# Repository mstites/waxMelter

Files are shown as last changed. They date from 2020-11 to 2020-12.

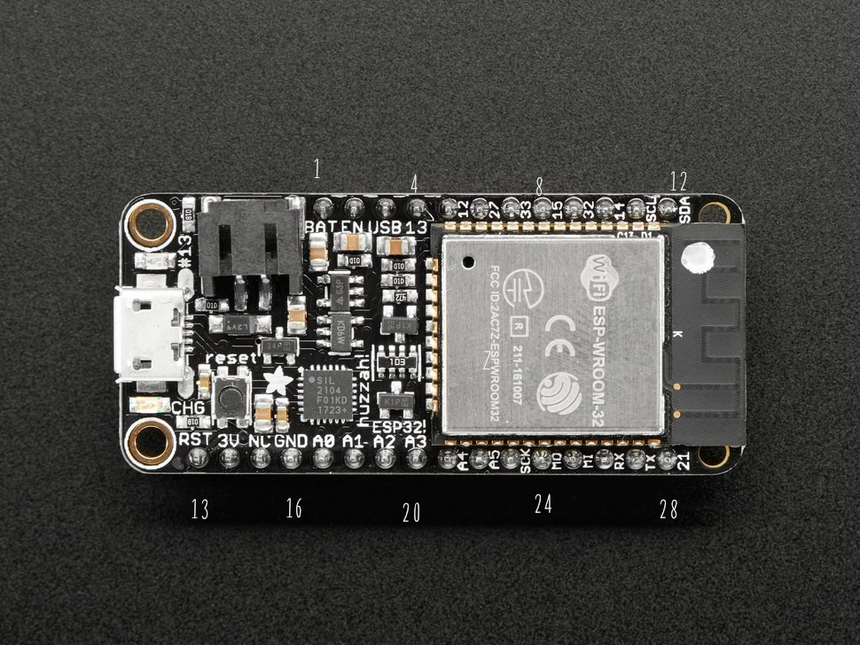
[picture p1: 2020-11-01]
schematic/microNumbering.png

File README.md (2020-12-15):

# waxMelter
Custom designed board and software for a bangbang controlled thermocouple feedback wax melter. Please see [project page](https://www.mstites.com/items/wax_melter.html) for more information.

## Overview
The board heats and maintains the temperature of a container of candle wax via controlling a hot plate with a relay power control. All code was written in C in an Arduino based environment for an Adafruit ESP32 Huzzah. There is a fully functional OLED and button UI and web based UI.

## Files and Notes
* For final software iteration please see [software/dualUi](software/dualUi). Software depends on the [espressif-esp32](https://github.com/espressif/arduino-esp32#using-through-arduino-ide) and [ESPAsyncWebServer](https://github.com/me-no-dev/ESPAsyncWebServer) libraries. Any other missing dependencies should be able to be installed through the Arduino IDE (eg [Button2](https://github.com/LennartHennigs/Button2), [RunningMedian](https://github.com/RobTillaart/RunningMedian)).
* Project proposal is located in [proposal](proposal). This was a project for [ENGR3499-02: Microcontrollers for the Real World](http://reifel.org/realworld/) taught by Stan Reifel at Olin College of engineering. Though this project was also a passion work as I [make many candles](http://trandleboutique.com).
* Final schematic, kicad files, and PCB files are located in [schematic](schematic). It should be noted that the final PCB I ended up with I had to make adjustments to. I had to disconnect the A1 to SENSOR_0 connection and reconnect SENSOR_0 to A2. The same would also have to be done with respect to A5 and SENSOR_1 (to some ADC1 pin). This is because the original pins, A1 and A5, I picked are connected to ADC2 on the ESP. Only ADC1 can be used while wifi is enabled ([see here for pin numbering](https://learn.adafruit.com/adafruit-huzzah32-esp32-feather/pinouts)).

## Parts List
* [Adafruit HUZZAH32](https://www.adafruit.com/product/3591)
* [Thermocouple Amplifier AD8495](https://www.adafruit.com/product/1778)
* [K Type Thermocouple](https://www.ebay.com/itm/1M-K-Type-Thermocouple-Sensor-Digital-Thermometer-Temperature-Meter-TK80-4JPL8/282896189061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)
* [Hot Plate](https://www.amazon.com/gp/product/B07MMT2SC5/ref=ask_ql_qh_dp_hza)
* [Outlet Power Relay](https://www.amazon.com/Iot-Relay-Enclosed-High-Power-Raspberry/dp/B00WV7GMA2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)
* [SPI OLED 128x64](https://www.amazon.com/UCTRONICS-SSD1306-Self-Luminous-Display-Raspberry/dp/B072Q2X2LL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)
* SPST Switch x6
* USB Power Supply
* Micro USB Cable
* LD1117V33 x2	
* 0.1uF Cermic Capacitor x6
* 10uF Electrolytic Capacitor x4
* 4.7K Resistor 1/8W x6
* 2 Pin Screw Terminal x2
Sockets:
* 16 pin x2
* 12 pin x2
* 4 pin x2

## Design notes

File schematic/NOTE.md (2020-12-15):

In my initial design, I did not realize that ADC #2 cannot be used while wifi is on with the ESP32. Both of my analog reads for the thermocouples in my design were on ADC #2. To remedy this in my design, I ran a jumper from SENSOR_0 to A2 and used a knife to take out the A1 path. I did not use the other channel, though a similar remedy could have been implemented.

I recommend in future iterations moving to A2 and A4 instead of A1 and A5 to avoid this issue.

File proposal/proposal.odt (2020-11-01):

Wax Melter Proposal

Maeve Stites

# Overview and Background

I am going to make a board to control a system to heat wax (used in candle making) to a specified temperature. I run a queer and trans candle shop (http://www.trandleboutique.com/) where I make and sell hand poured candles. One of the most variable and frustrating parts of the process is melting the wax. The wax has to be heated to a specific temperature to mix in dyes and scents. The wax is heated to a different temperature to pour into the candle containers. I currently do this over the stove in a double broiler system, where it is hard to regulate temperature. Differences as small as 5 degrees (F) can make a big difference in the performance of the wax.

The board will regulate the container temperature and monitor the temperature of the wax to help it reach the right temperature and stay there. It will control a hot plate, which will heat a container containing the wax. The board will use temperature monitoring, temperature control via a hot plate, and remote control through a web platform.

# Parts List

- Adafruit HUZZAH32 (https://www.adafruit.com/product/3591) - $20.95
- Thermocouple Amplifier AD8495 (https://www.adafruit.com/product/1778) - $11.95
- K Type Thermocouple (https://www.ebay.com/itm/1M-K-Type-Thermocouple-Sensor-Digital-Thermometer-Temperature-Meter-TK80-4JPL8/282896189061) - $5.75
- Hot plate (https://www.amazon.com/gp/product/B07MMT2SC5/ref=ask_ql_qh_dp_hza) - $22
- Outlet Power Relay (https://www.amazon.com/Iot-Relay-Enclosed-High-Power-Raspberry/dp/B00WV7GMA2) - $27
- OLED 128x64 Yellow Blue (https://www.amazon.com/UCTRONICS-SSD1306-Self-Luminous-Display-Raspberry/dp/B072Q2X2LL) - $7
- SPST Switch (https://www.digikey.com/en/products/detail/apem-inc/MJTP1230/1798037) - $0.10 X6
- USB Power Supply (https://www.adafruit.com/product/501) - $5.95
- Micro usb cable – Have
- LD1117V33 (https://www.digikey.com/en/products/detail/stmicroelectronics/LD1117V33/586012) - $0.55 X2
- 0.1uF Ceramic Capacitor (https://www.digikey.com/en/products/detail/vishay-beyschlag-draloric-bc-components/K104K15X7RF5TL2/286538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) - $0.23 X6
- 10uF Electrolytic Capacitor (https://www.digikey.com/en/products/detail/nichicon/UKL1C100KDD1TD/5699141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)- $0.27 X4
- 4.7K Resistor 1/8W (https://www.digikey.com/en/products/detail/stackpole-electronics-inc/CF18JT4K70/1741708) - $0.10 X6
- 2 Pin Screw Terminal (https://www.digikey.com/en/products/detail/phoenix-contact/1751248/2511016) - $1.26 X2
- Sockets - $3.5 total
  - 16 pin (https://www.digikey.com/en/products/detail/sullins-connector-solutions/PPPC161LFBN-RC/810188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) (micro) - $1.02 X2
  - 12 pin (https://www.digikey.com/en/products/detail/sullins-connector-solutions/PPPC121LFBN-RC/810184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) (micro) - $0.81 X2
  - 4 pin (https://www.digikey.com/en/products/detail/sullins-connector-solutions/PPPC041LFBN-RC/810176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) (amplifier and OLED) - $0.47 X2

Total = $111.38

# Implementation Plan

The core of the system is the Adafruit HUZZAH32. I chose this particular micro controller because of its integrated wifi module and common use in IoT device spaces. The ESP32 is an updated version of the popular ESP8266. And has more GPIOs and is faster, and the boards come in around the same price. This last part means there is lots of documentation and support online for communicating with the device over wifi and hosting a web page on the device.

The whole system will be controlled via a locally accessible web page broad-casted by the micro controller (my additional area of study). The website will contain the current temperature reading of the wax/container, the target temperature, and have a buttons for controlling the target temperature for the wax, as well as the power of the device. I am not currently planning on implementing a way to communicate with the micro controller remotely, as the use case of my board – making candles – means the user should be on the same local network.

A secondary user interface will be visible via an OLED panel. This will have temperature readings and target temperature information. The OLED will be connected over I2C. Buttons will be placed below the panel to interact via this secondary user interface.

The system will get temperature readings via the thermocouple connected via the thermocouple amplifier (AD8495). I am planning on building in two thermocouple channels, but only putting in components for one due to cost restrictions. With the one thermocouple, I can regulate the outside temperature of the container or the temperature of the wax. With a second thermocouple, I could also track the internal temperature of the wax in real time while tracking the temperature of the container.

The thermocouple will be connected via a 2 position screw terminal. The thermocouple amplifier will be connected to one ADC input channel.

To control the temperature of the wax, the board will control a hot plate. This will be done by flipping the outlet on and off via the Outlet Power Relay, connected via a digital i/o pin. The specific software implementation will come with time, but a basic bang/bang controller could work with the limits for when to flip the switch determined in testing. Some sort of PID loop could be implemented if this did not work well enough.

All of the modules support 3.3V logic. All power will be supplied by the usb adapter. Power will be stepped down for the micro by the onboard voltage regulator. The LD1117V33 will be used to power the OLED and the thermocouple modules.

### Resources

#### Wireless

Connecting ESP32 to Wifi Networking (https://circuits4you.com/2019/01/05/connecting-esp32-to-wifi-network/)

ESP32: Getting Started with Wifi (https://www.dfrobot.com/blog-948.html)

ESP32: Set Static IP (https://techtutorialsx.com/2020/04/21/esp32-arduino-set-static-ip-address/) (shouldn’t be necessary, but this resource has more wireless info)

#### Web

Controlling RGB Lights from ESP32 (https://diyusthad.com/2019/10/controlling-rgb-lights-from-esp32-web-server.html)

ESP32-CAM Take Photo and Display in Web Server (https://randomnerdtutorials.com/esp32-cam-take-photo-display-web-server/)

#### Thermocouple

Wiring a Thermocouple (https://learn.adafruit.com/thermocouple/wiring-a-thermocouple)

Power and Temperature Data Logger with ESP32 and AWS IOT (https://www.instructables.com/Power-and-Temperature-Data-Logger-With-ESP32-and-A/)

ESP32 and Max6675 Example (http://www.esp32learning.com/code/esp32-and-max6675-example.php)

Thermocouple Amplifier and K-Type Thermocouple Interface (https://www.instructables.com/Thermocouple-Amplifier-and-K-Type-Thermocouple-Int/)

#### OLED Display

Seller Recommend Library (https://github.com/supprot/ArducamSSD1306)

Included Documentation (https://www.uctronics.com/download/Amazon/U602602.pdf)

Text Only (Smaller) Library with Examples (https://github.com/greiman/SSD1306Ascii)

Adafruit 128x64 OLED Featherwing (https://learn.adafruit.com/adafruit-128x64-oled-featherwing/arduino-code)

Adafruit 1.3” (https://learn.adafruit.com/monochrome-oled-breakouts/downloads) – uses same text only library I am looking at using

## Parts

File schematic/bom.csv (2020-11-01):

Reference | Qnty | Value | Datasheet | Vendor Value
C1, C2, C4 | 3 | 0.1uF | https://www.vishay.com/docs/45171/kseries.pdf | DK: BC1084CT-ND
C3 | 1 | 10uF | https://katalog.we-online.de/pbs/datasheet/860020572003.pdf | DK: 732-8937-1-ND
J1 | 1 | Screw_Terminal_01x02 | https://media.digikey.com/PDF/Data%20Sheets/Phoenix%20Contact%20PDFs/1751248.pdf | DK: 277-5719-ND
OLED1 | 1 | .96_OLED | https://cdn-shop.adafruit.com/datasheets/SSD1306.pdf | Amazon
R1, R2 | 2 | 4.7K | https://www.seielect.com/catalog/sei-cf_cfm.pdf | DK: CF18JT4K70CT-ND
SW1 | 1 | PWR | https://media.digikey.com/pdf/Data%20Sheets/APEM%20Components%20PDFs/MJTP%20Series-6MM.pdf | DK: 679-2428-ND
SW2 | 1 | T+ | https://media.digikey.com/pdf/Data%20Sheets/APEM%20Components%20PDFs/MJTP%20Series-6MM.pdf | DK: 679-2428-ND
SW3 | 1 | T- | https://media.digikey.com/pdf/Data%20Sheets/APEM%20Components%20PDFs/MJTP%20Series-6MM.pdf | DK: 679-2428-ND
TC1, TC2 | 2 | Thermocouple | K Type Thermocouple | Ebay, Amazon
U1 | 1 | LD1117V33 | http://www.st.com/st-web-ui/static/active/en/resource/technical/document/datasheet/CD00000544.pdf | DK: 497-1491-5-ND
U2 | 1 | HUZZAH32_ESP32 | https://cdn-learn.adafruit.com/downloads/pdf/adafruit-huzzah32-esp32-feather.pdf?timestamp=1603059915 | Adafruit: 3591
U3, U4 | 2 | AD8495_Breakout | https://www.adafruit.com/product/1778 | Adafruit: 1778

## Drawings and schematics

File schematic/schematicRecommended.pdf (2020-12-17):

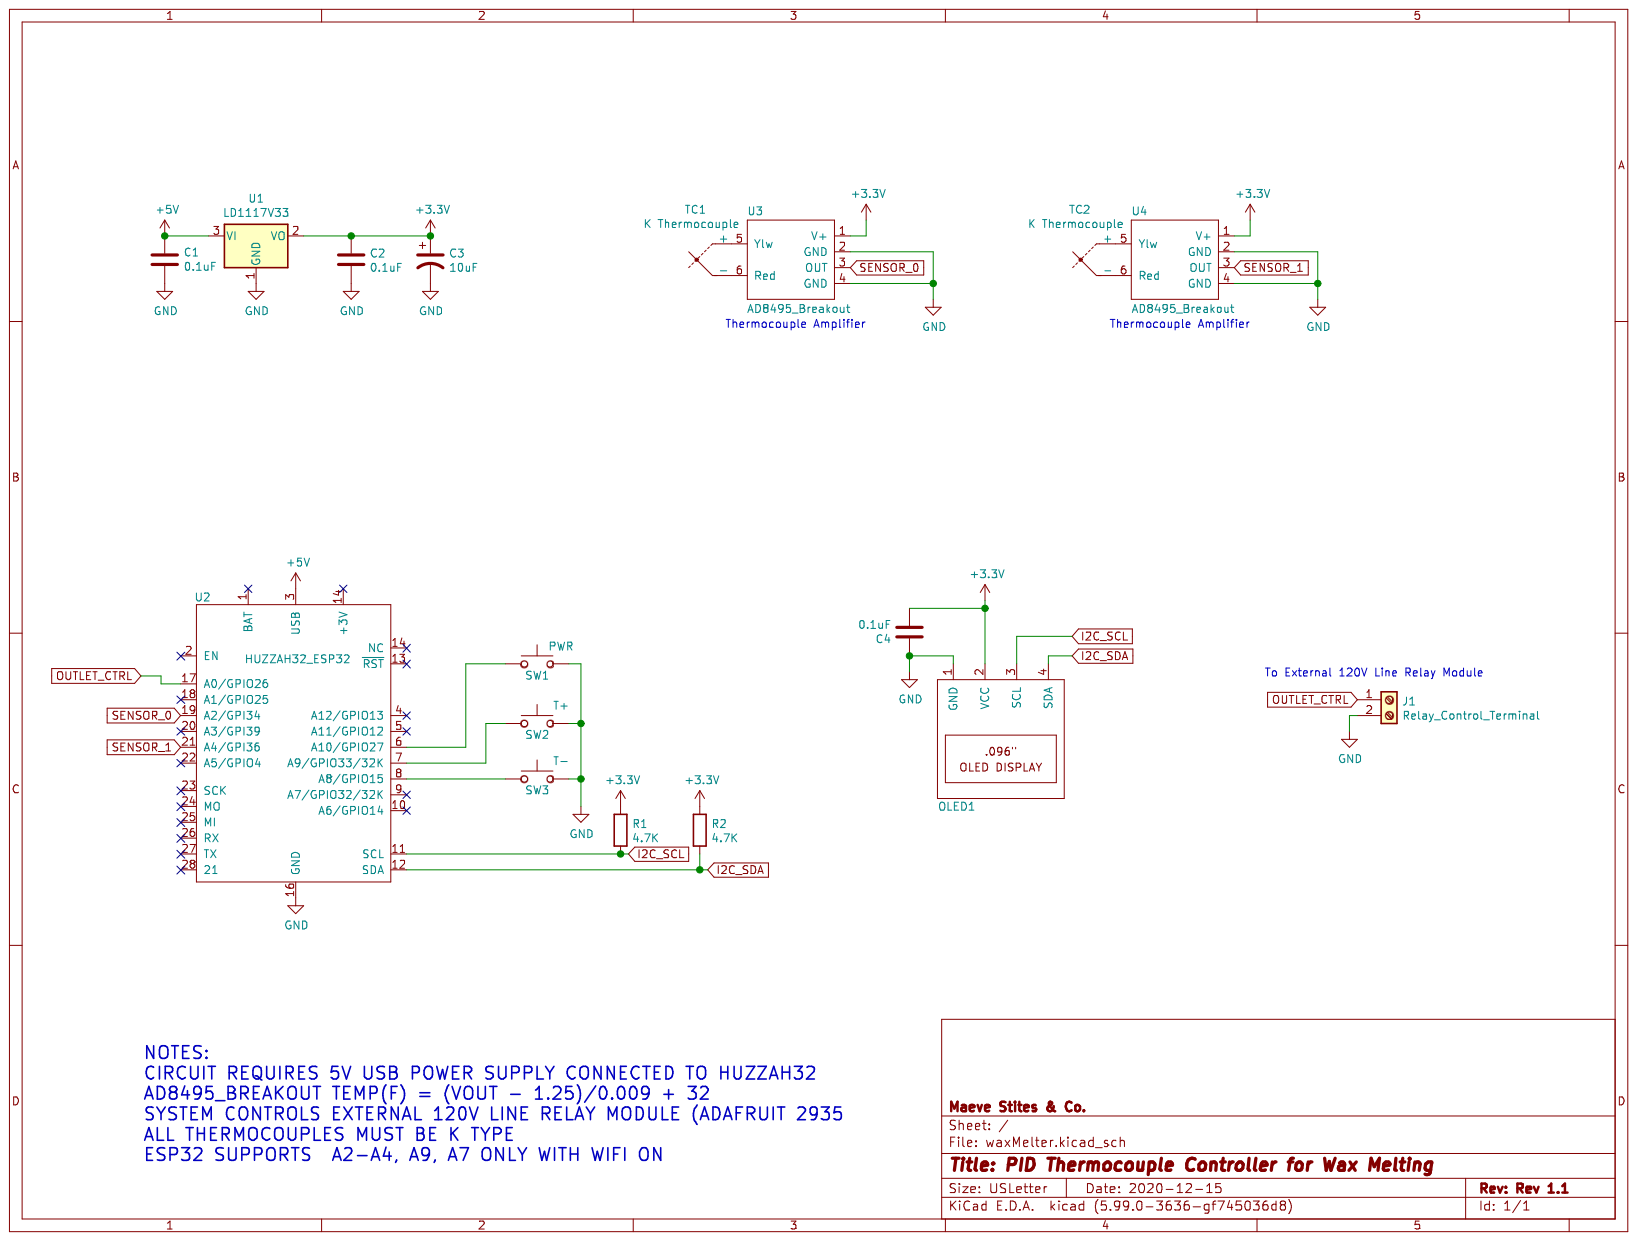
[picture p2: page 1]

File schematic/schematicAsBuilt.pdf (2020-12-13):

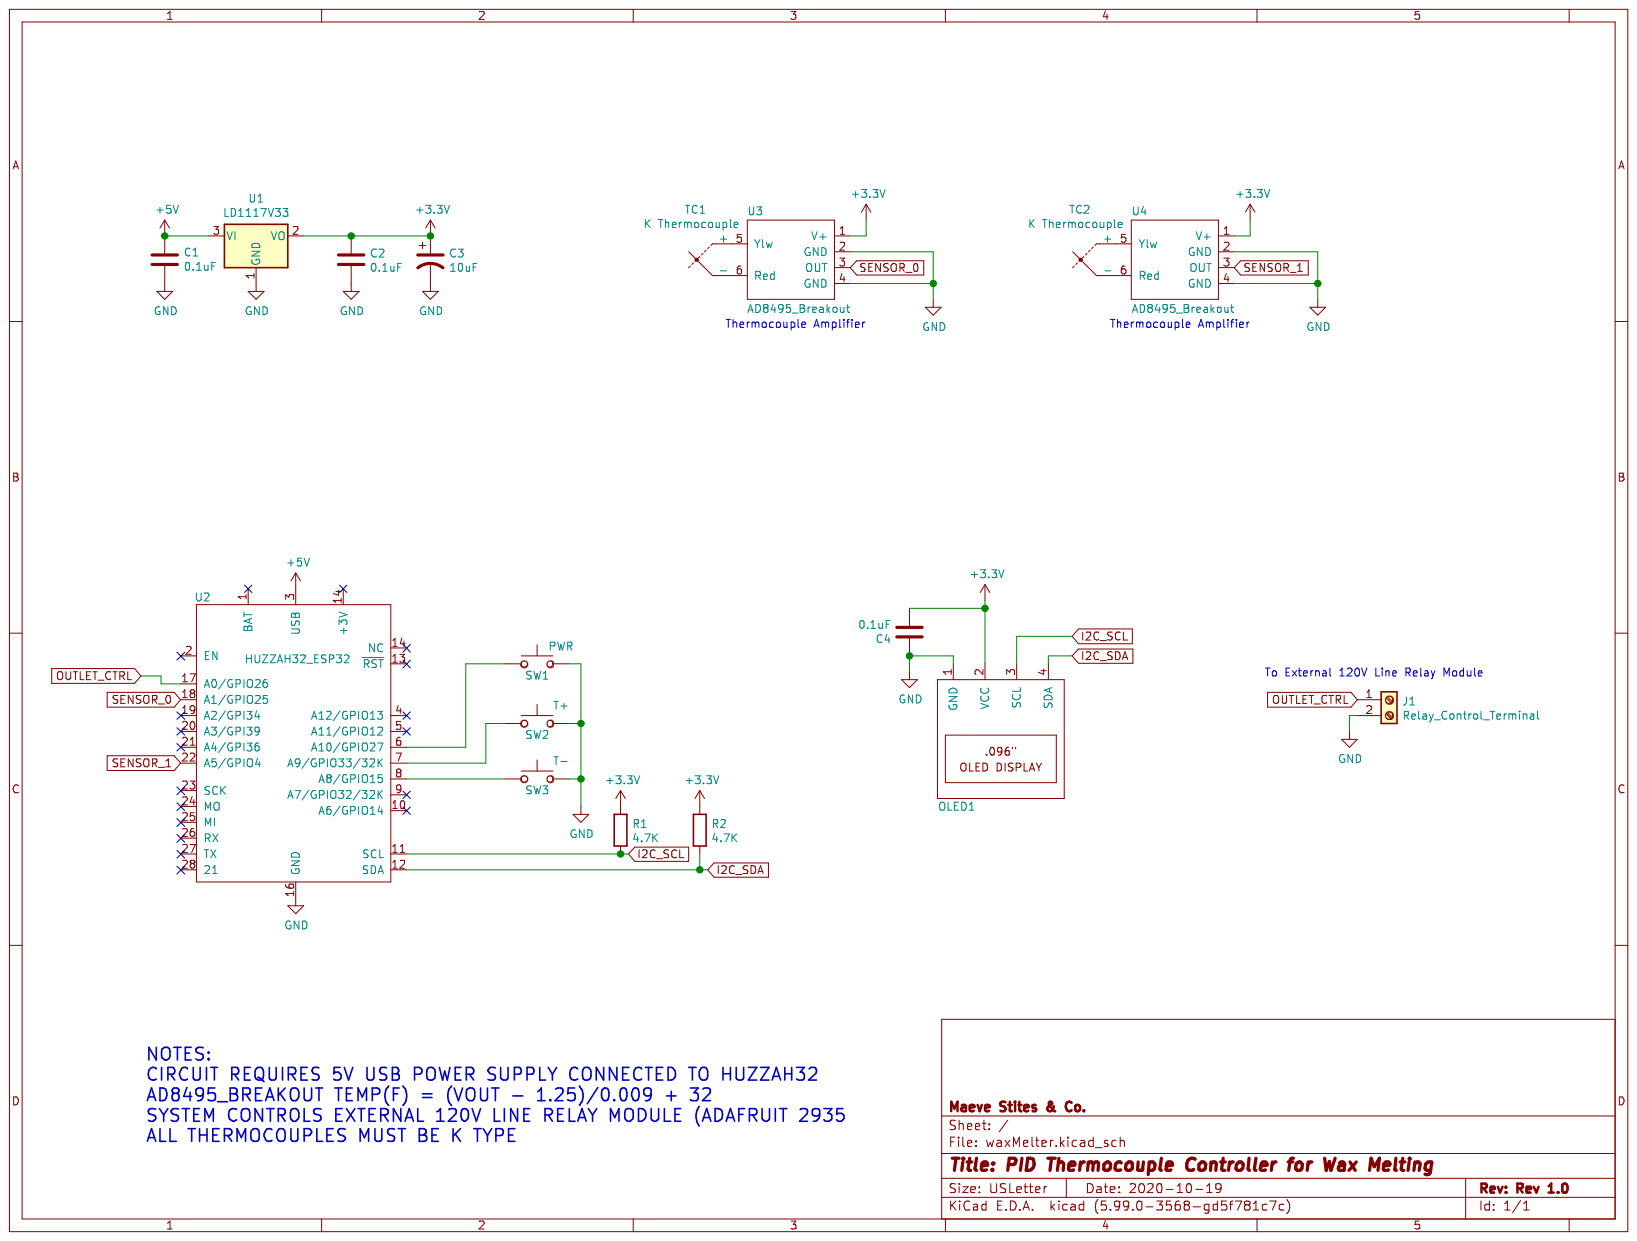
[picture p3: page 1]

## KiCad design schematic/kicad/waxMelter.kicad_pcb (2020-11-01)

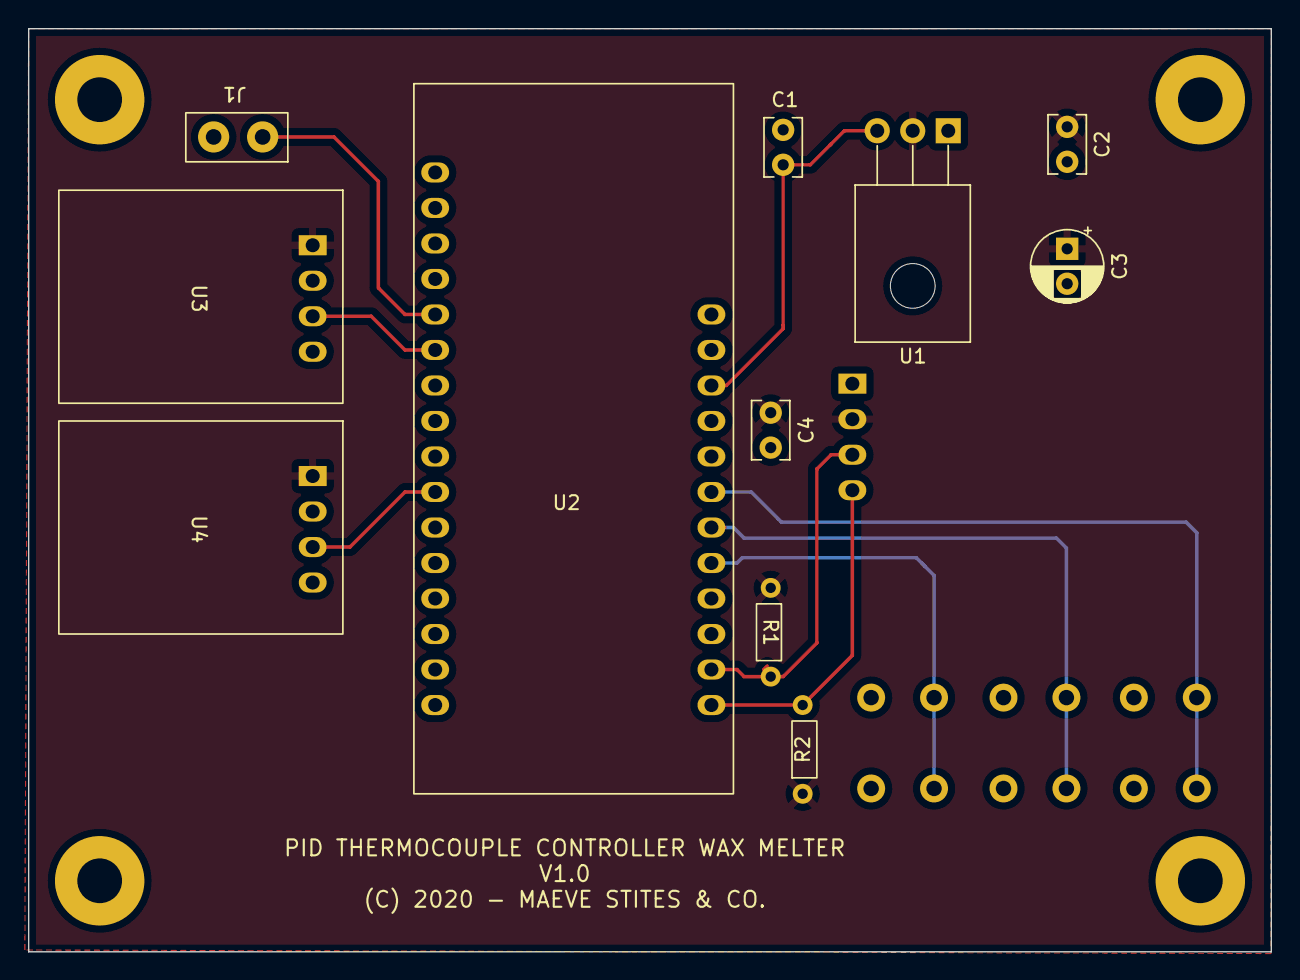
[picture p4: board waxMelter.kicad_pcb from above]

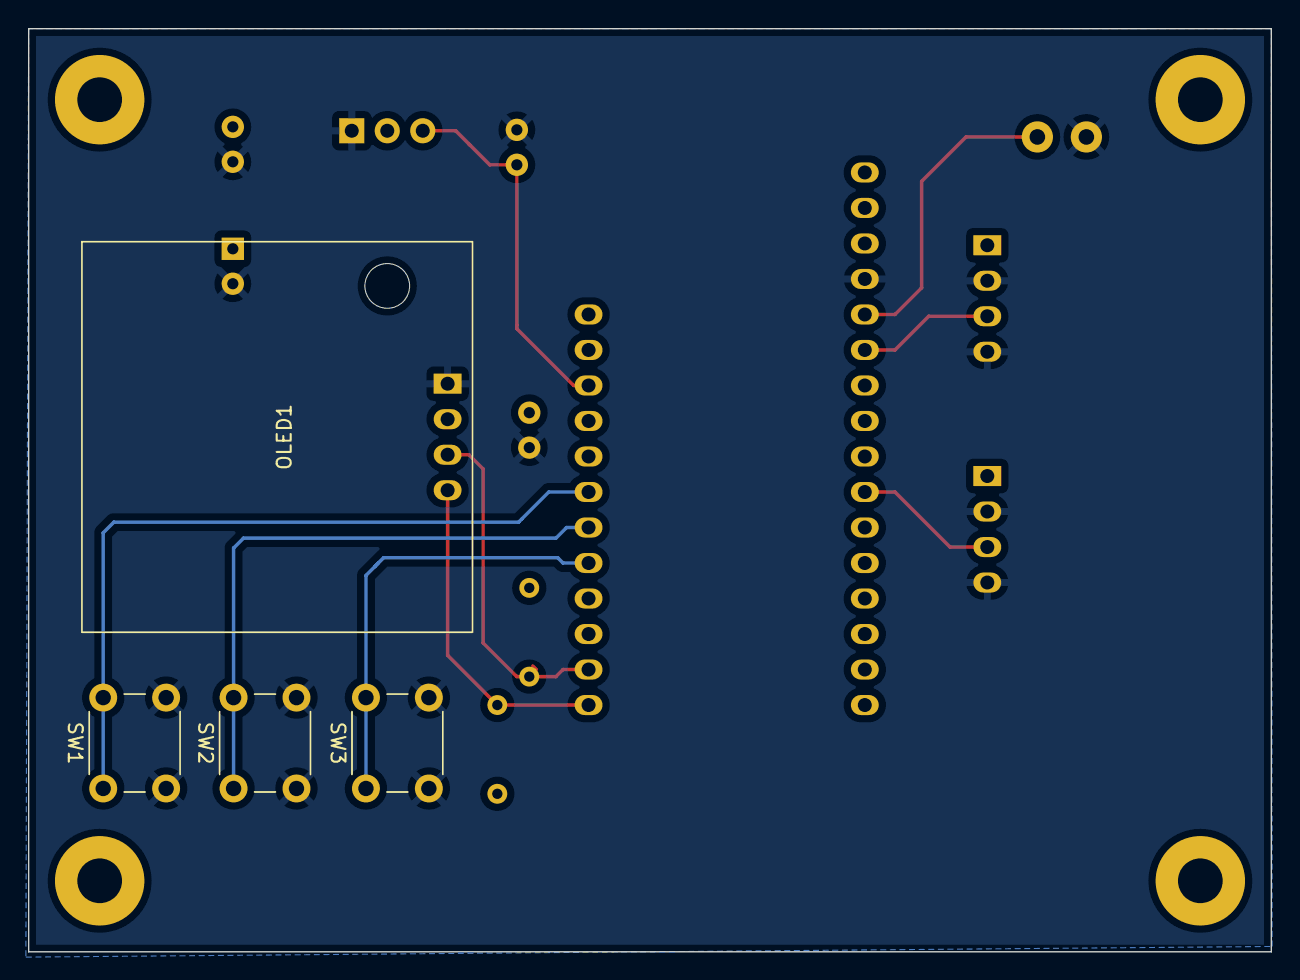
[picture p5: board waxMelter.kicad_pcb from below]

Board: 2 copper layers, 88.9 x 66.0 mm, 15 parts (4 on the bottom side), 11 nets.

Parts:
C1, C2, C4: 0.1uF; C_Rect_L4.0mm_W2.5mm_P2.50mm
C3: 10uF; CP_Radial_D5.0mm_P2.50mm
J1: Relay_Control_Terminal; 2PIN_SCREW
OLED1: .96_OLED; OLED
R1, R2: 4.7K; resistor 1-8
SW1: PWR; SW_PUSH_6mm
SW2: T+; SW_PUSH_6mm
SW3: T-; SW_PUSH_6mm
U1: LD1117V33; TO-126-3_Horizontal_TabDown
U2: HUZZAH32_ESP32; HUZZAH_ESP32
U3, U4: AD8495_Breakout; AD8495_amplifier

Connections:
+3V3: C2.1, C3.1, C4.2, OLED1.2 (VCC), R1.1, R2.1, U1.2 (VO), U3.1 (V+), U4.1 (V+)
+5V: C1.2, U1.3 (VI), U2.3 (USB)
GND: C1.1, C2.2, C3.2, C4.1, J1.2, OLED1.1 (GND), SW1.2, SW2.2, SW3.2, U1.1 (GND), U2.16 (GND), U3.2 (GND), U3.4 (GND), U4.2 (GND), U4.4 (GND)
I2C_SCL: OLED1.3 (SCL), R1.2, U2.11 (SCL)
I2C_SDA: OLED1.4 (SDA), R2.2, U2.12 (SDA)
unnamed: SW1.1, U2.6 (A10/GPIO27)
unnamed: SW2.1, U2.7 (A9/GPIO33/32K)
unnamed: SW3.1, U2.8 (A8/GPIO15)
OUTLET_CTRL: J1.1, U2.17 (A0/GPIO26)
SENSOR_0: U2.18 (A1/GPIO25), U3.3 (OUT)
SENSOR_1: U2.22 (A5/GPIO4), U4.3 (OUT)

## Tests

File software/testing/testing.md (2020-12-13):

# Testing
Information on preliminary testing I did on testing the functionality of the HUZZAH32, to help with final implementation.

## Environment Setup
1. Install Arduino IDE
2. Install [ESP32 Arduino Core](https://github.com/espressif/arduino-esp32)
3. Set board to "Arduino ESP32 Feather" and the upload speed to 921600

## Web
I tried a number of different example codes to try to avoid using the ESPAsyncWebServer and AsyncTCP packages. However, none of these were very stable or had the flexibility to meet my needs. I wanted to avoid these packages as they were larger in size and more complex than I originally thought necessary. They also were more difficult to learn than the other ESP web hosting options. 

I left my webui only test code, which relies on the ESPAsyncWebServer and AsyncTCP packages I ended up using. I used Rui Santos's guides and documentation to help me through much of this portion of the project.

I also left webControl.ino which is a piece of test code I worked the longest with that only relied on a simple WiFi package. However, this turned out to be difficult to use because the code had to be continually relooped.

## OLED
I am using [SSD1306Ascii](https://github.com/greiman/SSD1306Ascii) for OLED control. It can be installed via the built in Arduino package manager. I chose this particular package because of its low size requirements. It only supports ASCII characters, but that is the use case of my project. I can explore adding graphics at a later point. 
* helloWorld - simple helloWorld program
* template - line by line display using the maximum number of characters 
* oledUI - OLED only ui for wax melter

## Button
I am using [Button2](https://github.com/LennartHennigs/Button2) for my button management. It can be installed via the built in Arduino package manager. I am using it as it allows me to make my button management code cleaner. It supports a number of button functions including: debouncing, single/double/triple press tracking, and long press tracking. This gives me more options for making a user interface
* buttonTest - basic button functionality test with only built in functions
* Both button2single and button2singleSimple are built in examples, with the correct pin for my board selected.
* button2multiple is my preliminary implementation of managing multiple buttons and tracking long presses on the state button, which I plan to use for power off functionality.

## Relay
Relies on the Button2 package as seen is button testing. Pressing the select button toggles the status of the relay, when connected. The example is "relayControl".

## Temperature
Relies on the Button2 package as seen in testing. Pressing the up button takes a temperature sample. The example is "tempTest". Will need to calibrate the sensor and the curve.

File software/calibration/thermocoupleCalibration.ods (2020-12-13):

Analog Read | Voltage | Temp (F)
1674 | 1.34901098901099 | 134
1681 | 1.35465201465201 | 137
1680 | 1.35384615384615 | 137
1683 | 1.35626373626374 | 138
1690 | 1.36190476190476 | 140
1695 | 1.36593406593407 | 141
1698 | 1.36835164835165 | 142
1695 | 1.36593406593407 | 143
1701 | 1.37076923076923 | 144
1703 | 1.37238095238095 | 144
1710 | 1.37802197802198 | 146
1709 | 1.37721611721612 | 148
1715 | 1.38205128205128 | 149
1721 | 1.38688644688645 | 150
1726 | 1.39091575091575 | 152
1726 | 1.39091575091575 | 152
1742 | 1.40380952380952 | 154
1782 | 1.43604395604396 | 168
1811 | 1.45941391941392 | 173
1810 | 1.45860805860806 | 175
1821 | 1.46747252747253 | 180
1841 | 1.48358974358974 | 186
1881 | 1.51582417582418 | 195

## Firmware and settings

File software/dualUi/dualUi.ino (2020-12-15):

/////////////////////////////////////////////////////////////////

#include "Button2.h";
#include "RunningMedian.h"

// OLED
#include <Wire.h>
#include "SSD1306Ascii.h"
#include "SSD1306AsciiWire.h"
#define I2C_ADDRESS 0x3C // 7bit address, 8bit address is 0x78

// WEB UI
#include <WiFi.h>
#include <AsyncTCP.h>
#include <ESPAsyncWebServer.h>

/////////////////////////////////////////////////////////////////
// Pin Assignments //////////////////////////////////////////////
/////////////////////////////////////////////////////////////////
const int PLATE_POWER_PIN = A0;
const int TEMP_SENSOR_PIN = A2;

const int UP_BUTTON_PIN = A8;
const int SELECT_BUTTON_PIN = A9;
const int DOWN_BUTTON_PIN = A10;

/////////////////////////////////////////////////////////////////
// Instantiate objects  /////////////////////////////////////////
/////////////////////////////////////////////////////////////////

// BUTTONS //
Button2 up_button = Button2(UP_BUTTON_PIN);
Button2 select_button = Button2(SELECT_BUTTON_PIN);
Button2 down_button = Button2(DOWN_BUTTON_PIN);

// OLED //
SSD1306AsciiWire oled;
s
// MEDIAN FOR TEMPS //
RunningMedian t_samples = RunningMedian(10); // reset count every 10 data points

/////////////////////////////////////////////////////////////////
// State Values /////////////////////////////////////////////////
/////////////////////////////////////////////////////////////////
int currentTemp = 0;            // current temperature
int prevTemp = 0;               // last current temp
int targetTemp = 130;           // target temperature
int flipOffset = 2;             // temperature offset to flip power on/off

boolean heating = false;        // heating
boolean platePower = false;     // pwr to relay controlling hotplate
boolean heated = false;         // at temp

byte buttonMode = 1;            // 1 -> select, 2 -> adjust target temp
int lineSelection = 1;          // line selected on OLED
byte currentScreen = 0;         // 0-STANDBY, 1-HEATING

unsigned long currTime;                  // milis 

/////////////////////////////////////////////////////////////////
// Network Info  ////////////////////////////////////////////////
/////////////////////////////////////////////////////////////////

const char* ssid = "GoofZone";
const char* password = "9139122626";

/////////////////////////////////////////////////////////////////

void setup() {
  // open serial
  Serial.begin(9600);
  // init display
  Wire.begin();
  Wire.setClock(400000l);
  oled.begin(&Adafruit128x64, I2C_ADDRESS);
  oled.setFont(System5x7);
  standbyScreen(1, 1, currentTemp, targetTemp);

  // start web ui
  startWebUi();
//  startWifi();

  delay(1000);
  // set button handlers
  up_button.setTapHandler(upPress);
  select_button.setTapHandler(selectPress);
  down_button.setTapHandler(downPress);

  // configure pins
  pinMode(PLATE_POWER_PIN, OUTPUT);
  pinMode(TEMP_SENSOR_PIN, INPUT);

}

/////////////////////////////////////////////////////////////////

void loop() {
//  Serial.println(analogRead(TEMP_SENSOR_PIN));
  
  currTime = millis();
  
  // initalize constant checking
  up_button.loop();
  select_button.loop();
  down_button.loop();

  tempLogger();
  controlPlate();
  updateOLED();
  
}

/////////////////////////////////////////////////////////////////
// Button Loops /////////////////////////////////////////////////
/////////////////////////////////////////////////////////////////

void upPress(Button2& btn) {
    Serial.println("Up: Pressed");
    arrow(1);
}

void selectPress(Button2& btn) {
    unsigned int time = btn.wasPressedFor();
    if (time < 1000) {
        Serial.println("Select: Regular press");
        middle();
    } 
    else {
        Serial.println("Select: long press");
        Serial.println("Turning OFF");
        heating = false;
        platePower = false; // should be handled somewhere else
    }
}

void downPress(Button2& btn) {
    Serial.println("Down: Pressed");
    arrow(-1);
}

/////////////////////////////////////////////////////////////////
// Button Func/State Handler ////////////////////////////////////
/////////////////////////////////////////////////////////////////

// MIDDLE BUTTON
void middle(){
  if (buttonMode == 1){               // SELECT
    if (lineSelection == 1) {
       buttonMode = 2;                // change target temp
    }
    else if (currentScreen == 0) {
       changeScreen(1);               // go to heating screen
       heating = true; 
       heated = false;                // reset
    }
    else if (currentScreen == 1) {
       heating = false; 
       heated = false;                // reset
       changeScreen(0);               // go to heating screen     
    }
  }
  else if (buttonMode == 2){          // ADJUST
    buttonMode = 1;                   // back to select mode
  }
}

// BUTTOM/TOP BUTTON FUNCTIONALITY
void arrow(int dir){
  if (buttonMode == 1){               // SELECT
    refreshScreen(dir, currentTemp, targetTemp);
  }
  else if (buttonMode == 2){          // ADJUST
    targetTemp = targetTemp + dir;    // change target temp
    refreshScreen(0, currentTemp, targetTemp); // no selection change
  }
  Serial.println(lineSelection);
}

// CHANGE TO NEW SCREEN
void changeScreen(byte newScreen){
  if (currentScreen != newScreen) {
    currentScreen = newScreen;        // update global
    lineSelection = 1;                // reset counter
    refreshScreen(0, currentTemp, targetTemp);
  }
}

/////////////////////////////////////////////////////////////////
// OLED Display /////////////////////////////////////////////////
/////////////////////////////////////////////////////////////////

unsigned long oled_next = 0;

void updateOLED() {
    // if within five of target temp, update every temp
    if ((abs(targetTemp - currentTemp) <= 5) && (currentTemp != prevTemp)) { 
      refreshScreen(0, currentTemp, targetTemp);
      prevTemp = currentTemp;
    }
    else if (abs(currentTemp - prevTemp) >= 5) { // otherwise only for steps of 5
      refreshScreen(0, currentTemp, targetTemp);
      prevTemp = currentTemp;
    }
    if (currTime > oled_next) {
      oled_next = currTime + 500;
      checkHeatingStatus();
    }
}

void checkHeatingStatus() {
  // Checks if OLED is correct given status, and refreshes as needed
  // needed because of web UI
  if ((heating) && (currentScreen != 1)) {
    changeScreen(1);
  }
  else if (!(heating) && (currentScreen != 0)) {
    changeScreen(0);
  }
}

// WRITE SCREEN
void printScreen(String L1, String L2, String L3, String L4, String L5, String L6, String L7, String L8) {
    oled.clear();
    oled.println(L1);
    oled.println(L2);
    oled.println(L3);
    oled.println(L4);
    oled.println(L5);
    oled.println(L6);
    oled.println(L7);
    oled.println(L8);
}


// COMPUTE LOCATION (selction with limits)
int compSelection (int maxSel, int prevSel, int dir) {
    int sel;
    sel = prevSel - dir;
    if (sel > maxSel) {
      sel = maxSel;
    }
    else if (sel < 1) {
      sel = 1;
    }
    return(sel);
}

// REFRESH SCREEN
void refreshScreen(int dir, int temp, int target) { // should be done immediately
  if (currentScreen == 0) { // STANDBY
    lineSelection = standbyScreen(lineSelection, dir, temp, target);
  }
  else if (currentScreen == 1) { // heating
    lineSelection = heatingScreen(lineSelection, dir, temp, target);
  }
}

// STANDBY SCREEN - Screen 0
int standbyScreen(int prevSel, int dir, int temp, int target) {
    int maxSel = 2; 
    int selection = compSelection(maxSel, prevSel, dir);
    String arrow = String("`");
    String tempCurrent = String(temp);
    String tempTarget = String(target);
    String blank = String("");
    String L1 = String("STATUS: STANDBY");
    String L2 = String("WEB: " + String(WiFi.localIP().toString().c_str()));
    String L3 = String("Current temp      " + tempCurrent);
    String L4 = String("Temp target       " + tempTarget);
    if (selection == 1) {
        String L8 = String("Start heating       ");
        String L6 = String("Change Target Temp  " + arrow);
        printScreen(L1, L2, L3, L4, blank, L6, blank, L8);
    }
    else {
        String L8 = String("Start heating       " + arrow);
        String L6 = String("Change Target Temp  ");   
        printScreen(L1, L2, L3, L4, blank, L6, blank, L8);
    }
    return(selection);
}

// 1 SCREEN - Screen 1
int heatingScreen(int prevSel, int dir, int temp, int target) {
    int maxSel = 2; 
    int selection = compSelection(maxSel, prevSel, dir);
    String arrow = String("`");
    String tempCurrent = String(temp);
    String tempTarget = String(target);
    String blank = String("");
    String L1 = String("STATUS: HEATING");
    String L2 = String("WEB: " + String(WiFi.localIP().toString().c_str()));  
    String L3 = String("Current temp      " + tempCurrent);
    String L4 = String("Temp target       " + tempTarget);
    if (selection == 1) {
        String L6 = String("Change Target Temp  " + arrow);
        String L8 = String("Cancel/Exit         ");
        printScreen(L1, L2, L3, L4, blank, L6, blank, L8);
    }
    else {
        String L6 = String("Change Target Temp  ");
        String L8 = String("Cancel/Exit         " + arrow);
        printScreen(L1, L2, L3, L4, blank, L6, blank, L8);
    }
    return(selection);
}

/////////////////////////////////////////////////////////////////
// Temperature Management ///////////////////////////////////////
/////////////////////////////////////////////////////////////////

int t_count = 0;
unsigned long temp_count_next = 0;

// READ TEMP
int readTemp(){
//  float vOut;
//  vOut = analogRead(TEMP_SENSOR_PIN) * (3.3/4095); // 12 bit resolution
//  return vOut*362.44-353.23;
  return((0.2921*analogRead(TEMP_SENSOR_PIN)) - 353.233423);
}

// UPDATES CURRENT TEMP
void tempLogger(){
  if (currTime > temp_count_next) {
    t_samples.add(readTemp());
    t_count++;
    temp_count_next = currTime + 100;
    if (t_count == 10) {
       currentTemp = t_samples.getMedian();
       t_count = 0;
    }
  }
}

/////////////////////////////////////////////////////////////////
// Plate Control ////////////////////////////////////////////////
/////////////////////////////////////////////////////////////////

// CONTROL POWER VIA RELAY
void controlPlate() {
  if (heating){
    if ((currentTemp - targetTemp) >= flipOffset) {
      setPlatePower(false);
      heated = true;
    }
    else if (currentTemp <= (targetTemp - flipOffset)) {
      setPlatePower(true);
      heated = true;
    }
  }
  else if (platePower){ // off with plate on
      setPlatePower(false);
  }
}

// SET DESIRED STATE
void setPlatePower(boolean desired) {
   if (platePower == desired) {
       ; // do nothing
   }
   else if (desired == false){
    // set false, turn off 
    platePower = false;
    digitalWrite(PLATE_POWER_PIN, LOW);
   }
   else {
    // set true, turn on
    platePower = true;
    digitalWrite(PLATE_POWER_PIN, HIGH);    
   }
   Serial.print("Plate power: ");
   Serial.println(platePower);
}

/////////////////////////////////////////////////////////////////
// Web UI Values ////////////////////////////////////////////////
/////////////////////////////////////////////////////////////////

AsyncWebServer server(80);

// Pointers to the field values
const char* PARAM_INPUT_1 = "targTempInput";
const char* PARAM_INPUT_2 = "state";

// HTML CODE
const char INDEX_HTML[] PROGMEM = R"rawliteral(
<!DOCTYPE HTML><html><head>
  <title>Wax Melter Control</title>
  <meta name="viewport" content="width=device-width, initial-scale=1">
  <meta http-equiv="refresh" content="10">

  <!--STYLE INFO-->
  <style>
  html {font-family: Arial; display: inline-block; text-align: center;}
  h1 {font-size: 3.0rem;}
  h2 {font-size: 2.0rem;}
  h3 {font-weight: normal;}
  p {font-size: 1.0rem;}
  body {max-width: 600px; margin:0px auto; padding-bottom: 25px; padding-top: 25px;}
  .switch {position: relative; display: inline-block; width: 120px; height: 68px} 
  .switch input {display: none}
  .slider {position: absolute; top: 0; left: 0; right: 0; bottom: 0; background-color: #ccc; border-radius: 6px}
  .slider:before {position: absolute; content: ""; height: 52px; width: 52px; left: 8px; bottom: 8px; background-color: #fff; -webkit-transition: .4s; transition: .4s; border-radius: 3px}
  input:checked+.slider {background-color: #b30000}
  input:checked+.slider:before {-webkit-transform: translateX(52px); -ms-transform: translateX(52px); transform: translateX(52px)}
  </style>
  </head><body>

  <!--STATUS INDICATORS-->
  <h1>Wax Melter</h1> 
  <p style="font-style: italic;">Page refreshes every 10 seconds</p>
  <h2>Temp Status</h2>
  <h3>Current Temperature: %CURR_TEMP% &deg;F</h3>
  <h3>Target Temperature: %TARG_TEMP% &deg;F</h3>
  <h2>Control</h2>
  <!--TARGET TEMP-->
  <h3>New target: </h3>
    <form action="/update">
    <input type="number" step="1" name="targTempInput" value="%NEW_TARGET%" required>
    <input type="submit" value="Submit">
  </form>
  <!--BUTTON SLIDER-->
  %HEAT_SLIDER%
  <script>function toggleCheckbox(element) {
    var xhr = new XMLHttpRequest();
    if(element.checked){ xhr.open("GET", "/update?output="+element.id+"&state=1", true); }
    else { xhr.open("GET", "/update?output="+element.id+"&state=0", true); }
    xhr.send();
  }
  </script>
</body></html>)rawliteral";

/////////////////////////////////////////////////////////////////
// Web UI Support Functions /////////////////////////////////////
/////////////////////////////////////////////////////////////////

void notFound(AsyncWebServerRequest *request) {
  request->send(404, "text/plain", "Not found");
}

// Translate C variable to HTML button look
String outputState(){
  if(heating){
    return "checked";
  }
  else {
    return "";
  }
}

// Assign HTML placeholder values vars
String processor(const String& var){
  //Serial.println(var);
  if(var == "CURR_TEMP"){
    return String(currentTemp); // current temp status
  }
  else if(var == "TARG_TEMP"){
    return String(targetTemp); // target temp status
  }
  else if(var == "NEW_TARGET"){
    return String(targetTemp); // new target value in field
  }
  else if(var == "HEAT_SLIDER"){
    String buttons = "";
    buttons += "<h3>Heating:</h3><label class=\"switch\"><input type=\"checkbox\" onchange=\"toggleCheckbox(this)\" id=\"2\" " + outputState() + "><span class=\"slider\"></span></label>";
    return buttons;
  }
  return String();
}

/////////////////////////////////////////////////////////////////
// Web UI Startup ///////////////////////////////////////////////
/////////////////////////////////////////////////////////////////

void startWifi() {
  WiFi.mode(WIFI_STA);
  WiFi.begin(ssid, password);
  if (WiFi.waitForConnectResult() != WL_CONNECTED) {
    Serial.println("WiFi Failed!");
    return;
  }
}

void printAddress() {
  Serial.println();
  Serial.print("ESP IP Address: http://");
  Serial.println(WiFi.localIP());
}

void serverInit() {
  // DEFAULT BEHAVIOR
  server.on("/", HTTP_GET, [](AsyncWebServerRequest *request){
    request->send_P(200, "text/html", INDEX_HTML, processor);
  });

  // USER UPDATE BEHAVIOR
  server.on("/update", HTTP_GET, [] (AsyncWebServerRequest *request) {
    if (request->hasParam(PARAM_INPUT_1)) {           // if target temp change
      targetTemp = (request->getParam(PARAM_INPUT_1)->value()).toInt();
      Serial.println(String(targetTemp));
    }
    else if (request->hasParam(PARAM_INPUT_2)) {      // if heating status change
      int input = (request->getParam(PARAM_INPUT_2)->value()).toInt();
      if (input == 1){
        heating = true;
      }
      else {
        heating = false;
      }
      Serial.println(input);     
    }
    // Page after user inputs: 
    request->send(200, "text/html", "Request sent to your wax melter.<br><a href=\"/\">Return to Home Page</a>");
  });
  server.onNotFound(notFound);
  server.begin();
}

char startWebUi() {
  startWifi();
  printAddress();
  serverInit();
}


/////////////////////////////////////////////////////////////////

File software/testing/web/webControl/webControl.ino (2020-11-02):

#include <WiFi.h>
#include <analogWrite.h>
 
// Replace with your network credentials
const char* ssid     = "GoofZone";
const char* password = "9139122626";
 
// Set web server port number to 80
WiFiServer server(80);
 
// Variable to store the HTTP request
String header;
 
// Assign output variables to GPIO pins
const int redPin = 26;
const int greenPin = 27;
const int bluePin = 25;
 
int greenValue = 0;
int redValue = 0;
int blueValue = 0;
 
String redValueString = String(redValue);
String greenValueString = String(greenValue);
String blueValueString = String(blueValue);
 
void setup() {
  Serial.begin(115200);
 
  // Connect to Wi-Fi network with SSID and password
  Serial.print("Connecting to ");
  Serial.println(ssid);
  WiFi.begin(ssid, password);
  while (WiFi.status() != WL_CONNECTED) {
    delay(500);
    Serial.print(".");
  }
  // Print local IP address and start web server
  Serial.println("");
  Serial.println("WiFi connected.");
  Serial.println("IP address: ");
  Serial.println(WiFi.localIP());
  server.begin();
 
  analogWriteResolution(8);
}
 
void loop(){
  WiFiClient client = server.available();   // Listen for incoming clients
 
  if (client) {                             // If a new client connects,
    Serial.println("New Client.");          // print a message out in the serial port
    String currentLine = "";                // make a String to hold incoming data from the client
    while (client.connected()) {            // loop while the client's connected
      if (client.available()) {             // if there's bytes to read from the client,
        char c = client.read();             // read a byte, then
        Serial.write(c);                    // print it out the serial monitor
        header += c;
        if (c == '\n') {                    // if the byte is a newline character
          // if the current line is blank, you got two newline characters in a row.
          // that's the end of the client HTTP request, so send a response:
          if (currentLine.length() == 0) {
            // HTTP headers always start with a response code (e.g. HTTP/1.1 200 OK)
            // and a content-type so the client knows what's coming, then a blank line:
            client.println("HTTP/1.1 200 OK");
            client.println("Content-type:text/html");
            client.println("Connection: close");
            client.println();
 
            if(header.indexOf("GET /-r") >=0 ) redValue -=1;
            else if(header.indexOf("GET /+r") >=0) redValue +=1;
            else if(header.indexOf("GET /+g") >=0) greenValue +=1;
            else if(header.indexOf("GET /-g") >=0) greenValue -=1;
            else if(header.indexOf("GET /+b") >=0)  blueValue +=1;
            else if(header.indexOf("GET /-b") >=0) blueValue -=1;
            else if(header.indexOf("GET /Red") >=0) if(redValue == 0) redValue = 254; else redValue = 0;
            else if(header.indexOf("GET /Green") >=0) if(greenValue == 0) greenValue = 254; else greenValue = 0;
            else if(header.indexOf("GET /Blue") >=0) {if(blueValue == 0) blueValue = 254; else blueValue = 0;}
 
            
            analogWrite(redPin,redValue);
            analogWrite(bluePin,blueValue);
            analogWrite(greenPin,greenValue);
 
            redValueString = String(redValue);  
            greenValueString = String(greenValue);
            blueValueString = String(blueValue);
 
            // Display the HTML web page
            client.println("<!DOCTYPE html><html>");
            client.println("<head><meta name=\"viewport\" content=\"width=device-width, initial-scale=1\">");
            client.println("<link rel=\"icon\" href=\"data:,\">");
            // CSS to style the on/off buttons 
            client.println("<link rel=\"stylesheet\" href=\"https://maxcdn.bootstrapcdn.com/bootstrap/3.4.0/css/bootstrap.min.css\">");
            
            client.println("</head>");
            
            // Web Page Heading
            
            client.println("<center>");
            client.println("<body><h1>ESP32 RGB Web Server</h1>"); 
            client.println("<br>");
 
            client.println("<a href = \" /+r \" ");
            if(redValue == 254)
            client.println("<button type=\"button\" class=\"btn btn-primary btn-md disabled\">+</button>"); 
            else
            client.println("<button type=\"button\" class=\"btn btn-primary btn-md\">+</button>"); 
            client.println("</a>");
 
            client.println("<a href = \" /Red\" ");
            client.println("<button type=\"button\" class=\"btn btn-primary btn-md\">RED(" + redValueString + ")</button>");  
            client.println("</a>");
            
            client.println("<a href = \" /-r \" ");
            if(redValue == 0)
            client.println("<button type=\"button\" class=\"btn btn-primary btn-md disabled\">-</button>");  
            else
            client.println("<button type=\"button\" class=\"btn btn-primary btn-md\">-</button>");  
            client.println("</a>");
 
            client.println("<br>");
            client.println("<br>");
 
            client.println("<a href = \" /+g \" ");
            if(greenValue == 254)
            client.println("<button type=\"button\" class=\"btn btn-primary btn-md disabled\">+</button>"); 
            else
            client.println("<button type=\"button\" class=\"btn btn-primary btn-md\">+</button>"); 
            client.println("</a>");
            
            client.println("<a href = \" /Green \" ");
            client.println("<button type=\"button\" class=\"btn btn-primary btn-md\">GREEN(" + greenValueString + ")</button>");  
            client.println("</a>");
 
            client.println("<a href = \" /-g \" ");
            if(greenValue == 0)
            client.println("<button type=\"button\" class=\"btn btn-primary btn-md disabled\">-</button>");  
            else
            client.println("<button type=\"button\" class=\"btn btn-primary btn-md\">-</button>");
            client.println("</a>");
 
            client.println("<br>");
            client.println("<br>");
 
            client.println("<a href = \" /+b \" ");
            if(blueValue == 254)
            client.println("<button type=\"button\" class=\"btn btn-primary btn-md disabled\">+</button>");  
            else
            client.println("<button type=\"button\" class=\"btn btn-primary btn-md\">+</button>");  
            client.println("</a>");
 
            client.println("<a href = \" /Blue \" ");
            client.println("<button type=\"button\" class=\"btn btn-primary btn-md\">BLUE(" + blueValueString + ")</button>");  
            client.println("</a>");
 
            client.println("<a href = \" /-b \" ");
            if(blueValue == 0)
            client.println("<button type=\"button\" class=\"btn btn-primary btn-md disabled\">-</button>");  
            else
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

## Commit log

2020-11-01 Add schematic documentation
    [bom.csv]
2020-11-01 Add kicad information
    [waxMelter-B_Cu.gbr, waxMelter-B_Mask.gbr, waxMelter-B_Paste.gbr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]
2020-11-19 Remove unnecessary reset pin
2020-11-19 Basic button functionality test
2020-11-19 Start experimentation with button2 package for button management
2020-11-19 Update notes to include button updates
2020-11-19 Clean up codee for specific use case
2020-11-19 Complete relay test code
2020-11-19 Complete temperature testing
2020-11-29 Add selection control with buttons
2020-12-02 Add heating page
2020-12-02 Add live temperature reporting
2020-12-02 Add relay control
2020-12-02 Fix current temp refresh
    [oledUi.ino]
2020-12-09 Change global variable names to camel case
2020-12-09 Cut down to just one input field
2020-12-09 Update heating base on slider result
2020-12-13 Add calibration data
    [rawData.csv, thermocoupleCalibration.ods]
2020-12-13 Move calibration data to software dir
    [rawData.csv, thermocoupleCalibration.ods]
2020-12-13 Update schematic to match kicad
2020-12-13 Add new calibration curve
2020-12-15 Set adjusted pins post board refresh
2020-12-15 Add recommended schematic with notes on what happened
2020-12-17 Add schematic recommended
2020-12-17 Add updated kicad files
    [waxMelter.kicad_sch]

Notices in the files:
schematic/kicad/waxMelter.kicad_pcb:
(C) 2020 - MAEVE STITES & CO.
